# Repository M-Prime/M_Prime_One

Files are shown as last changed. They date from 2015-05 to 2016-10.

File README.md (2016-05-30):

# M Prime One

M Prime One is a free 3D printer intended to be simple, low-cost and easy to build and operate.

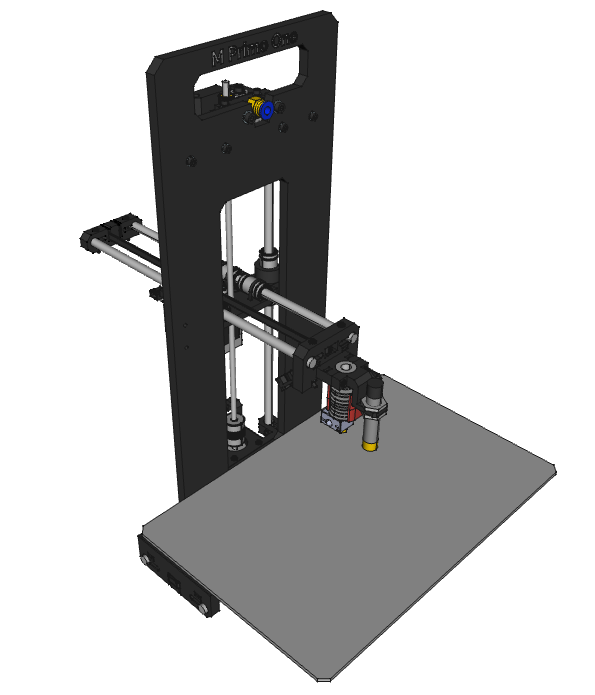
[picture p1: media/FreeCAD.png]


With the M Prime One, we have designed a 3D printer focusing on three main points:

* **Free design**. The printer have been designed from scratch in a free 3D software: FreeCAD. All the files have been published under the less restrictive license we have found (CC BY 4.0). This way anybody can download the files, modify them and use them for their own purposes.
* **Simplicity**. The design has few different parts (for example, cold bed, 4 motors, just two types of screws and one type of radial bearings) in an effort to reduce building complexity, cost and maintenance.
* **Documentation**. Apart from the files, you can find the printer firmware, list of materials, slicing profiles... in this repository, receive support in our [Q&A site](http://mprime.io/questions/) and soon read the complete assembly manual in the [manuals repository](https://github.com/M-Prime/M_Prime_One_manuals).

## Features

The features of the M Prime One are:

* Printing surface: 200x150x150mm.
* 1.75mm bowden extruder.
* Compatible with any hotend with 12mm diameter mount.
* Magnetic bed, easy to place and remove.
* Auto-level system with inductive/capacitive sensor.
* Cable management integrated in the design
* Integrated electronics holder (compatible with RAMPS, can be adapted to any other board)
* Optional LCD holder (compatible with Smart Controller)

## How to start building your M Prime One

* Download all the fabrication files (`.stl` for 3D printing and `.dxf` for laser/CNC cut) following our [fabrication file guide](documentation/fabrication_files.md).
* Check the complete part list is the Bill Of Materials, or [BOM](documentation/BOM.md).
* You can use the [assembled FreeCAD model](m_prime_one.fcstd) to help you build the machine or if you are comfortable installing modules in FreeCAD see the animated assembly files in our [manuals repository](https://github.com/M-Prime/M_Prime_One_manuals) (soon we will provide assembly videos).

And you can take a look at our [How to build an M Prime One guide](http://mprime.io/how-to-build-an-m-prime-one/), source some of the parts from our store and help the project =)

## License

The files of this 3D printer project have been released under the Creative Commons Attribution 4.0 license. This license lets you modify and share the sources for any purpose, even commercial, with the only requeriment of giving credit to the author.

Feel free to take a look at the files, modify them for your own uses, create new parts, etc. If you do so, I would be very happy if you let me know of your projects. Also, if possible, share them with the community with this or other free license.

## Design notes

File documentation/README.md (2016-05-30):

# Documentation

## Where is the Bill Of Materials

Check the complete part list is the Bill Of Materials: [BOM](documentation/BOM.md).

## Where are the fabrication files?

Download all the fabrication files (`.stl` for 3D printing and `.dxf` for laser/CNC cut) following our [fabrication file guide](documentation/fabrication_files.md).

## Assembling the M Prime One

You can use the [assembled FreeCAD model](m_prime_one.fcstd) to help you build the machine or if you are comfortable installing modules in FreeCAD see the animated assembly files in our [manuals repository](https://github.com/M-Prime/M_Prime_One_manuals) (soon we will provide assembly videos).

## Support

You can receive support from us and our community at:

* Q&A site: http://mprime.io/questions/
* Google+ community, for discussion and support: https://plus.google.com/u/0/communities/108084856251985677965

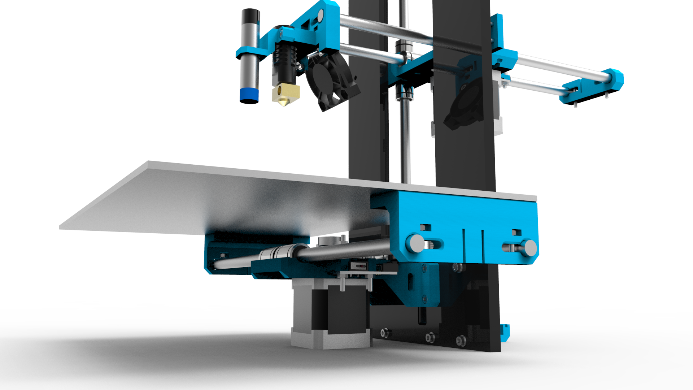
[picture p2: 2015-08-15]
media/renders_pre_v1.0/M Prime One.38.png

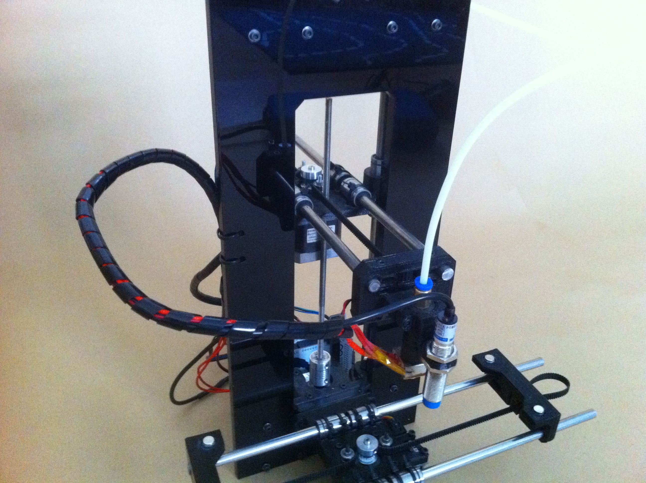
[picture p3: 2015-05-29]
media/2015-05-26 17.56.42.jpg

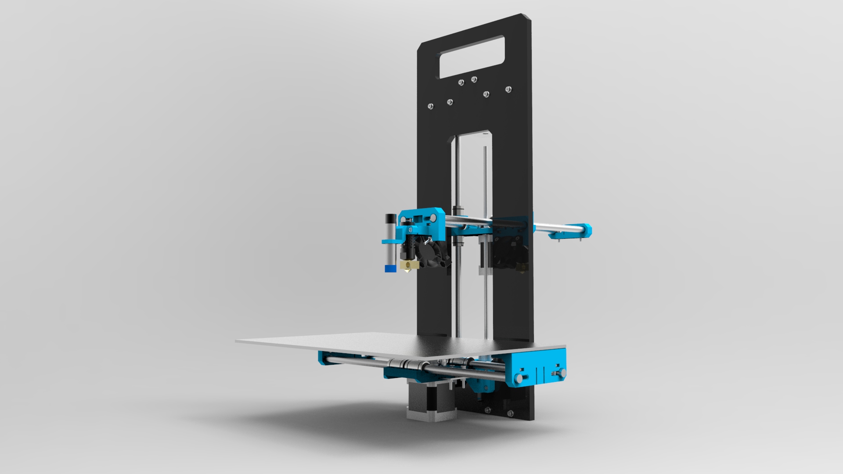
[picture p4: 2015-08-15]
media/renders_pre_v1.0/M Prime One.30.jpg

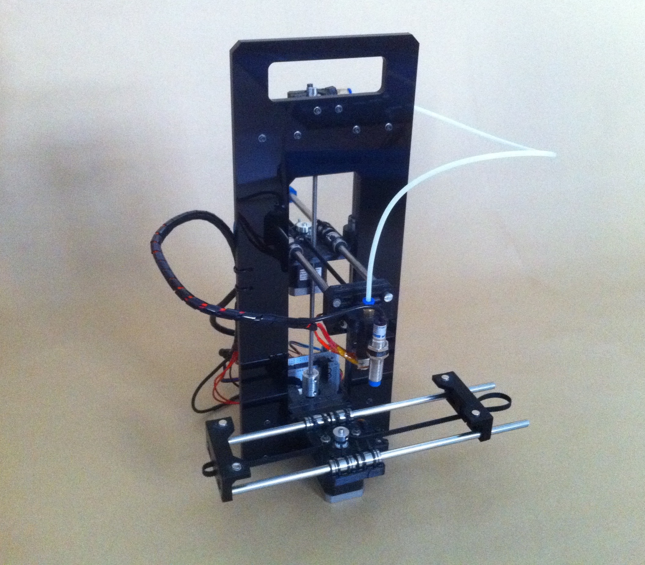
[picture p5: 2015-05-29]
media/2015-05-26 17.56.34 edited.jpg

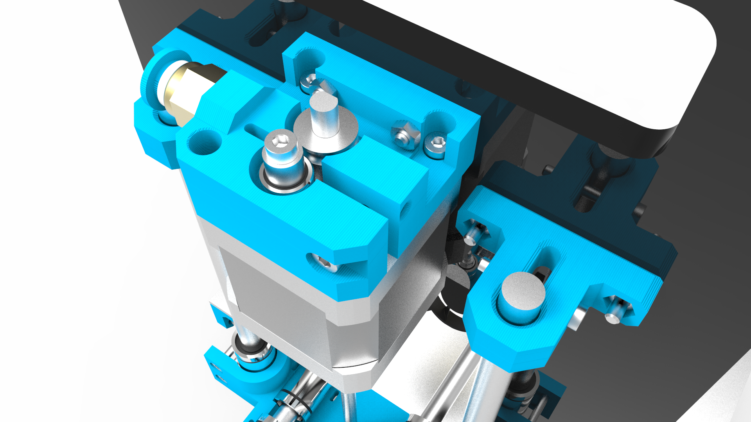
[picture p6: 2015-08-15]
media/renders_pre_v1.0/M Prime One.40.png

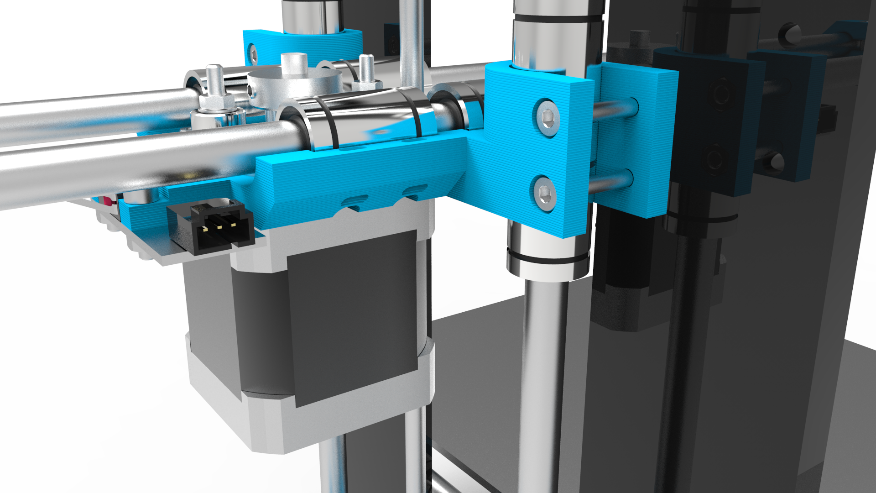
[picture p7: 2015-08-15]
media/renders_pre_v1.0/M Prime One.36.png

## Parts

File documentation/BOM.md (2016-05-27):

# M Prime One BOM

| Part | Quantity |  Unit | Notes |
| --- | --- | ----- | --- |
| NEMA 17 Motor | 4 | unit  | |
| Mechanical endstop v1.8  | 2 | unit  | |
| LM8UU linear bearing | 12 | unit  | |
| 623ZZ bearing | 9 | unit  | |
| GT2 belt | 1 | meter | |
| GT2 belt pulley | 2 | unit  | |
| Flexible shaft coupler | 1 | unit  | |
| M3x20 | 100 | unit  | More than necessary |
| M3x10 | 100 | unit  | More than necessary |
| M3 nut | 100 | unit  | More than necesary |
| M3 washer | 100 | unit  | More than necesary |
| M5 nut | 1 | unit  | |
| MK7 drive gear | 1 | unit  | |
| Bowden pneumatic fitting | 1 | unit  | Can be substituted with a M4 nut it using the hex nut version of the extruder |
| Frame | 1 | unit  | |
| Bed | 1 | unit  | 295x195x3mm aluminium/dibond plate. |
| Magnets | 4 | unit  | |
| 40x40mm fan | 1 | unit  | |
| Inductive sensor | 1 | unit  | LJ12A3-4-Z/BY |
| Rods | 1 | set | Detailed below |
| Printed parts | 1 | set | Detailed below |
| Hotend | 1 | unit  | ‎Any hotend with a Ø12mm mount should be compatible. Tested with J-Head |
| Electronics | 1 | set | |
| Power source | 1 | unit  | A 60W laptop-type power source is compact and has proven been enough |

## Rods
			
| Rods | Quantity | Length |
| --- | --- | --- |
| X 8mm smooth rod  | 2 | 300mm  |
| Y 8mm smooth rod  | 2 | 280mm  |
| Z 8mm smooth rod  | 2 | 365mm  |
| Z M5 threaded rod | 1 | 230mm  |
			
## Printed parts
	
| Printed parts | Quantity | Notes |
| --- | --- | --- |
| bowden_extruder | 1 | Use the hex nut version for attaching the bowden cable with a M4 nut |
| hotend_and_probe_holder | 1 | Needs support |
| printer_head | 1 | |
| smooth_rod_holder | 4 | |
| x_axis_end | 2 | |
| x_motor_support | 1 | |
| y_rear_end | 1 | |
| yz_carriage | 1 | Use the yz_carriage_fixed.stl file that fixes mesh problems |
| z_motor_support | 1 | |
| arduino_holder | 2 | Optional. Compatible with Arduino+RAMPS electronics |
| lcd_holder_left | 1 | Optional. Compatible with Smart Controller LCD |
| lcd_holder_right | 1 | Optional. Compatible with Smart Controller LCD |
| tool_holder | 1 | Optional. Use if you want a tool holder in the front of the printer  |

## Spreadsheet version

An online, spreadsheet version of this BOM can be accessed in the URL https://docs.google.com/spreadsheets/d/17mDN-wsaQ2GuqwfJa5OUW5vtk42V1e22lN0ufY5h_80/edit?usp=sharing. Feel free to copy the document and make your own list.

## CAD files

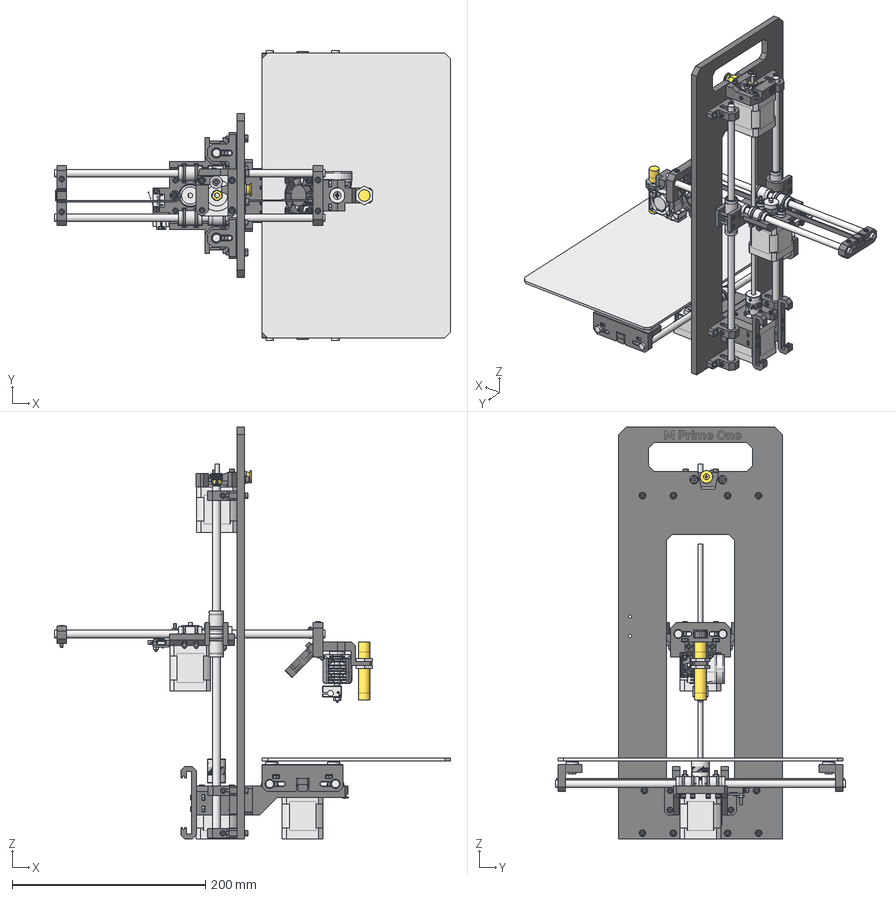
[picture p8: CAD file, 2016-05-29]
m_prime_one.fcstd
409.6 x 300.0 x 426.0 mm
nema_17_motor_01
frame_01
5x5mm_shaft_coupler_01
z_threaded_rod_01
pp_z_motor_support_01
m3x10_iso4762_bolt_01
m3x10_iso4762_bolt_02
m3x10_iso4762_bolt_03
m3x10_iso4762_bolt_04
pp_x_motor_support_01
pp_smooth_rod_holder_01
pp_smooth_rod_holder_02
m3_iso4032_nut_01
m3_iso4032_nut_02
m3_iso4032_nut_03
m3_iso4032_nut_04
m3_iso4032_nut_05
m3_iso4032_nut_06
m3_iso4032_nut_07
m3_iso4032_nut_08
m3_iso4032_nut_09
m3_iso4032_nut_10
m3_iso4032_nut_11
m3_iso4032_nut_12
m3_iso4032_nut_13
m3_iso4032_nut_14
m3_iso4032_nut_15
m3_iso4032_nut_16
m3_iso4032_nut_17
m3_iso4032_nut_18
pp_arduino_holder_01
pp_arduino_holder_02
m3_iso7089_washer_01
m3_iso7089_washer_02
m3_iso7089_washer_03
m3_iso7089_washer_04
m3_iso7089_washer_05
m3_iso7089_washer_06
m3x20_iso4762_bolt_01
m3x20_iso4762_bolt_02
m3x20_iso4762_bolt_03
m3x20_iso4762_bolt_04
m3x20_iso4762_bolt_05
m3x20_iso4762_bolt_06
m3x20_iso4762_bolt_07
m3x20_iso4762_bolt_08
m3x20_iso4762_bolt_09
m3x20_iso4762_bolt_10
m3x20_iso4762_bolt_11
m3x20_iso4762_bolt_12
m3x20_iso4762_bolt_13
m3x20_iso4762_bolt_14
z_smooth_rod_01
z_smooth_rod_02
m3x20_iso4762_bolt_15
m3x20_iso4762_bolt_16
m3x20_iso4762_bolt_17
m3x20_iso4762_bolt_18
nema_17_motor_02
m3x10_iso4762_bolt_05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

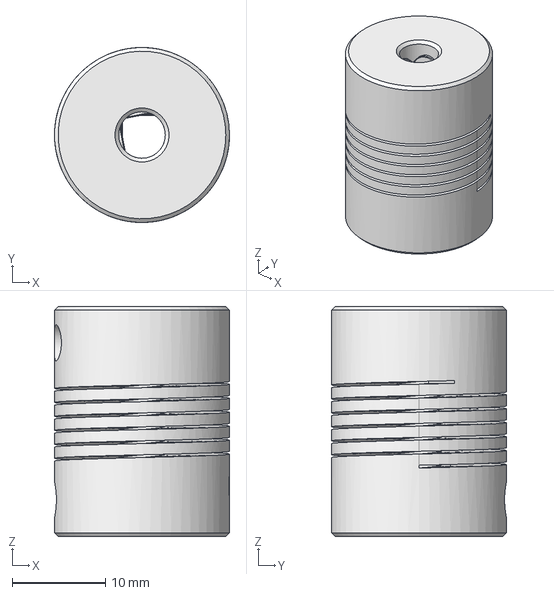
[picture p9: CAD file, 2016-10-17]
parts/5x5mm_shaft_coupler/5x5mm_shaft_coupler_views.FCStd
18.8 x 18.8 x 24.7 mm

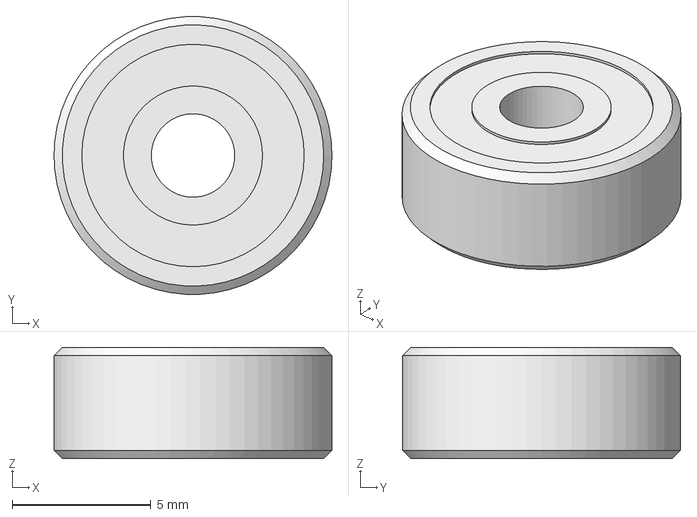
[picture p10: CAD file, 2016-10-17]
parts/623zz_bearing/623zz_bearing_views.FCStd
10.0 x 9.99 x 4.00 mm

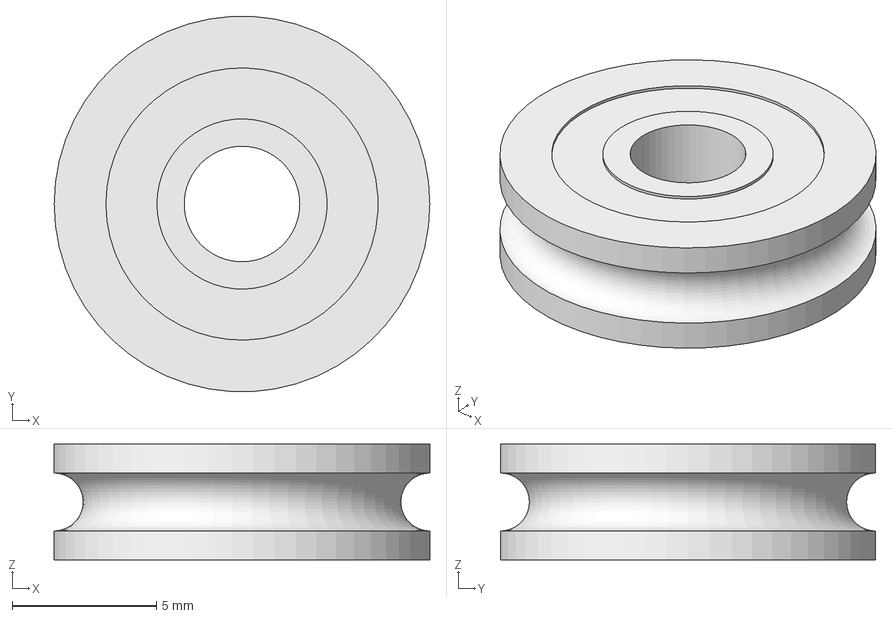
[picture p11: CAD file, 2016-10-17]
parts/624uu_bearing/624uu_bearing_views.FCStd
13.0 x 13.0 x 4.00 mm

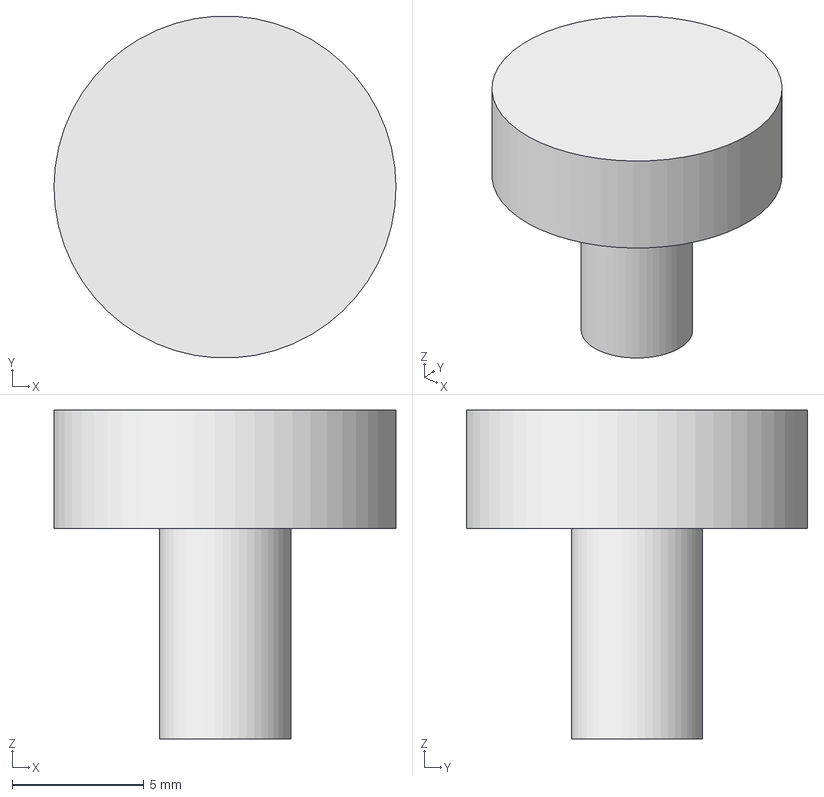
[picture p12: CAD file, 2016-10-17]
parts/bed_magnet/bed_magnet_views.FCStd
13.0 x 13.0 x 12.5 mm

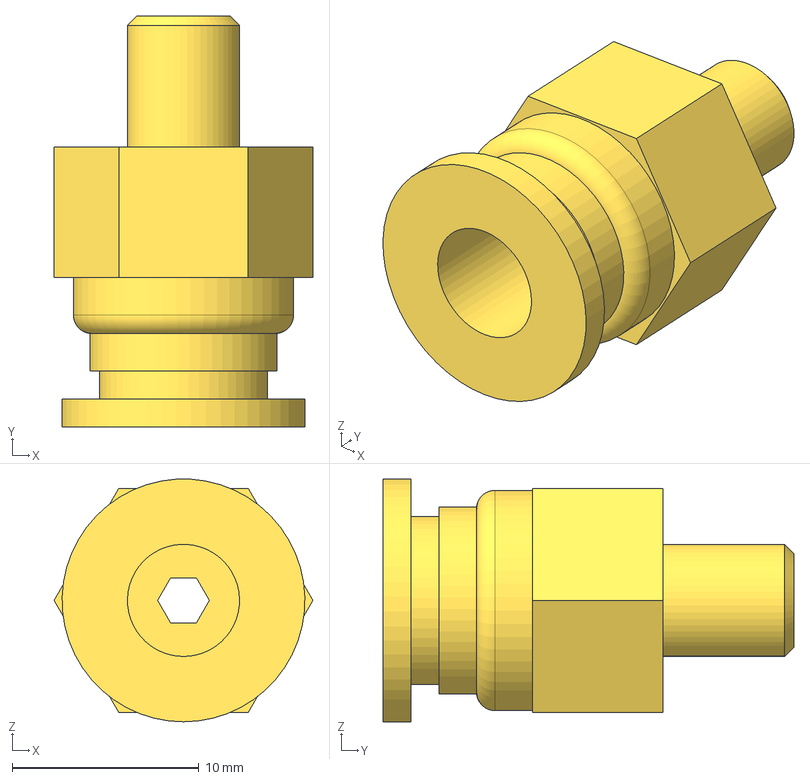
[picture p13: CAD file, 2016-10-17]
parts/bowden_fitting/bowden_fitting_views.FCStd
13.9 x 22.0 x 13.0 mm

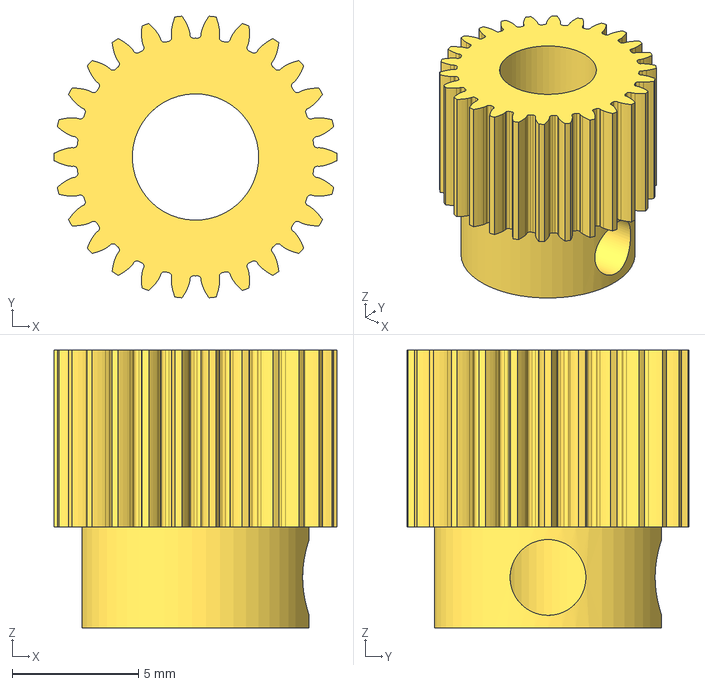
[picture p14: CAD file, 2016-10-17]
parts/drive_gear/drive_gear_views.FCStd
11.2 x 11.2 x 11.0 mm

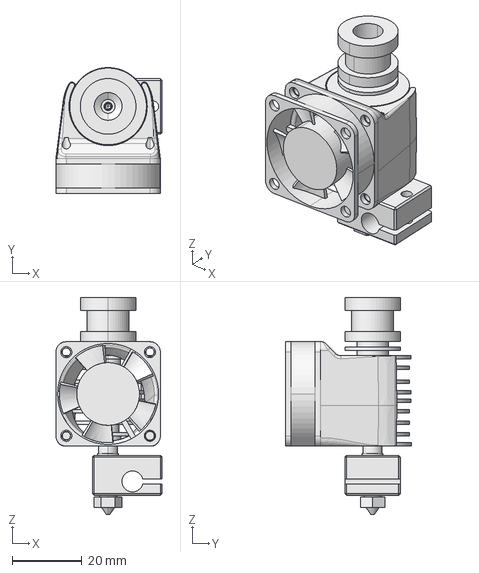
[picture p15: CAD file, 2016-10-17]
parts/e3d_lite6_hotend/e3d_lite6_hotend_views.FCStd
30.5 x 36.2 x 62.3 mm

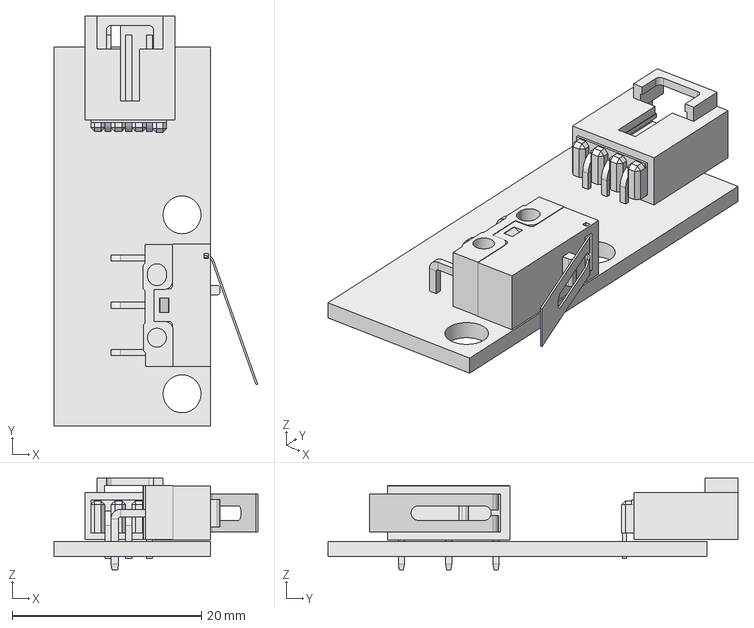
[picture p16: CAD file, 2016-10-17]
parts/endstop/endstop_views.FCStd
21.5 x 43.3 x 9.70 mm

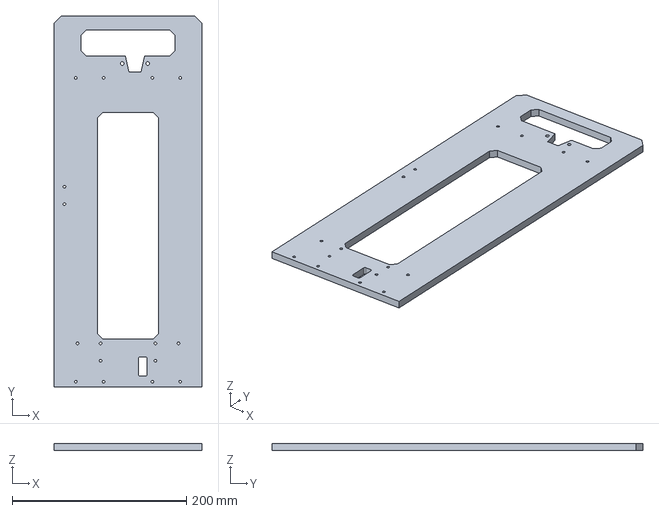
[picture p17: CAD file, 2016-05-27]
parts/frame/alternate_versions/frame_without_engraving.fcstd
170.0 x 426.0 x 8.00 mm

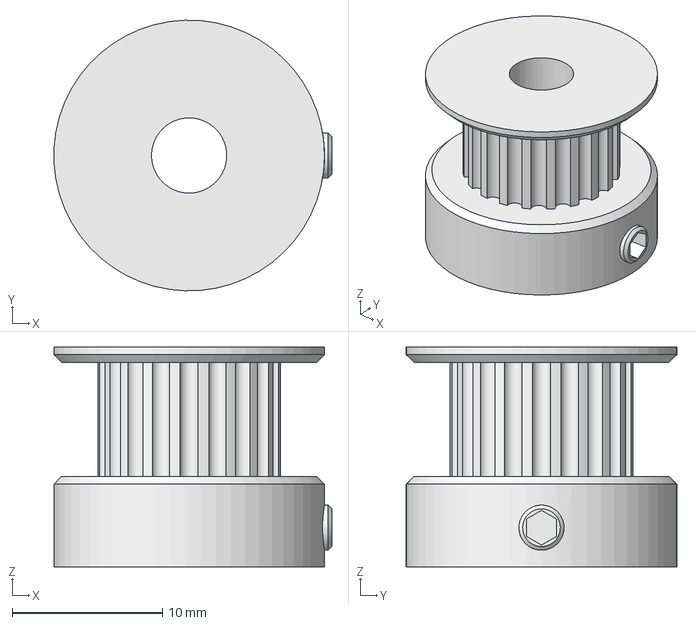
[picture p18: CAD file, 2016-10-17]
parts/gt2_pulley/gt2_pulley_views.FCStd
18.5 x 18.0 x 14.6 mm

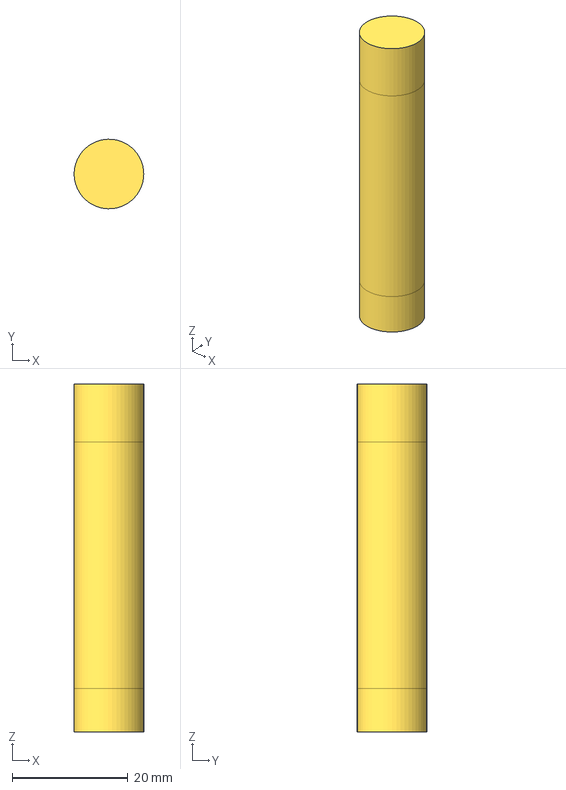
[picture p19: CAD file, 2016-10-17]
parts/inductive_sensor/inductive_sensor_views.FCStd
12.0 x 12.0 x 60.0 mm

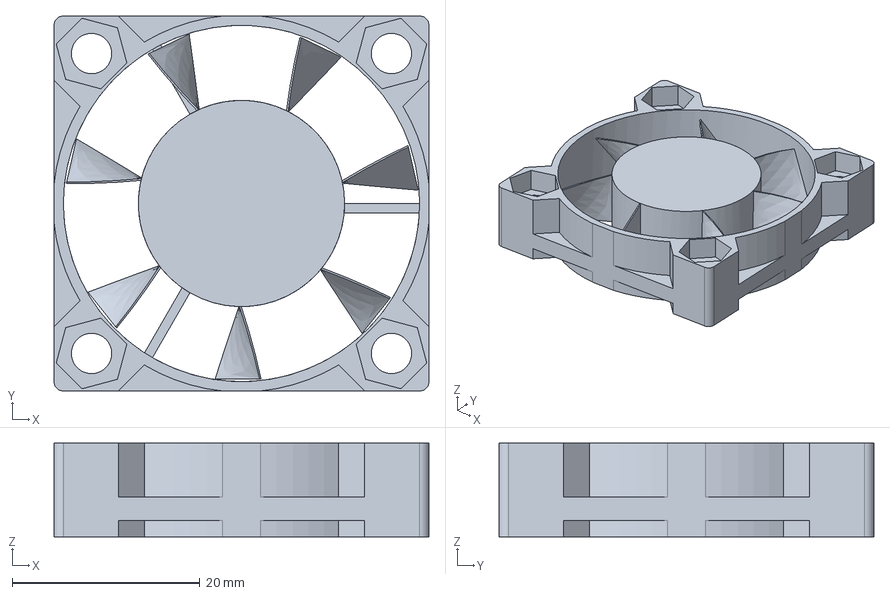
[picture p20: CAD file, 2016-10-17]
parts/layer_fan/layer_fan_views.FCStd
40.0 x 40.0 x 10.0 mm

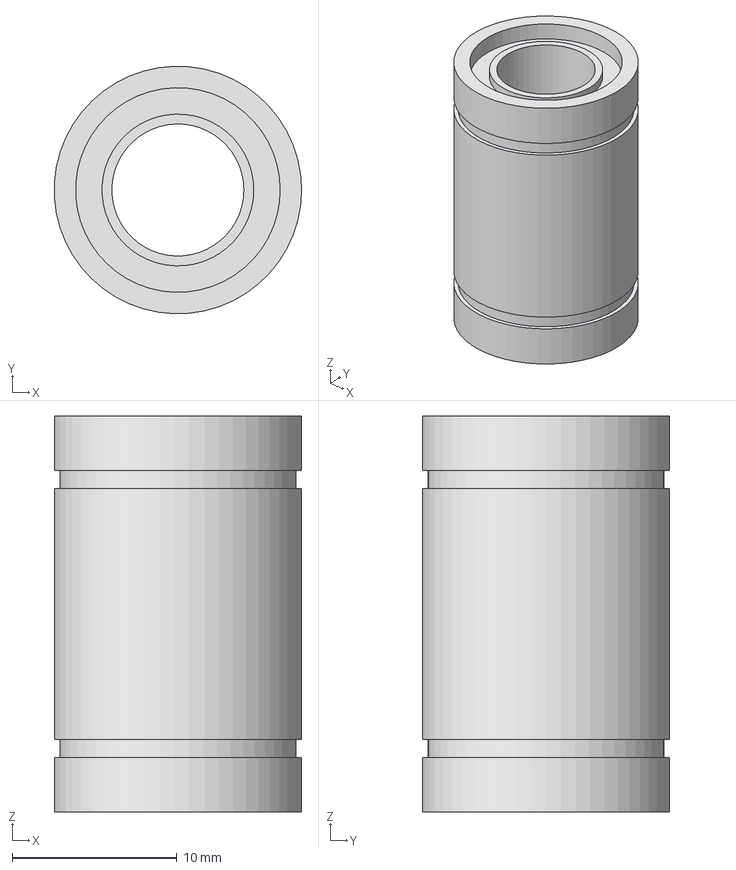
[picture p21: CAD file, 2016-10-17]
parts/lm8uu_linear_bearing/lm8uu_linear_bearing_views.FCStd
15.0 x 15.0 x 24.0 mm

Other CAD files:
parts/frame/frame_views.FCStd
parts/nema_17_motor/nema_17_motor_views.FCStd
parts/pp_arduino_holder/pp_arduino_holder_views.FCStd
parts/pp_hotend_and_probe_holder/pp_hotend_and_probe_holder_views.FCStd
parts/5x5mm_shaft_coupler/5x5mm_shaft_coupler.fcstd
parts/623zz_bearing/623zz_bearing.fcstd
parts/624uu_bearing/624uu_bearing.fcstd
parts/bed_magnet/bed_magnet.fcstd
parts/bowden_fitting/bowden_fitting.fcstd
parts/drive_gear/drive_gear.fcstd
parts/e3d_lite6_hotend/e3d_lite6_hotend.fcstd
parts/endstop/endstop.fcstd
parts/frame/alternate_versions/frame_without_engraving.dxf
parts/frame/frame.dxf
parts/frame/frame.fcstd
parts/gt2_pulley/gt2_pulley.fcstd
parts/inductive_sensor/inductive_sensor.fcstd
parts/inductive_sensor_nut/inductive_sensor_nut.fcstd
parts/inductive_sensor_nut/inductive_sensor_nut_views.FCStd
parts/layer_fan/layer_fan.fcstd
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

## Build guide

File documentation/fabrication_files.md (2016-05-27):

# M Prime One fabrication files

This is a document to help you find all the fabrication files in the M Prime One repository, files that are used to produce some of the parts of the printer: the printed parts and the files for laser cutting or routing the frame and the bed.

All the files are located in the `parts` directory of this repository, this file only contains all the links in one place. 

## Printed parts

All the printed parts are under the `parts` directories in the subdirectories that contain the prefix "pp_". There are also some optional parts that you can find in the `parts_optional` directory, including a beta bowden extruder that you can try if you don't want to use the PTSone extruder (however the extruder hasn't been fully tested and we cannot guarantee that it will perform reliably). We provide `.stl` files for the printed parts.

This is the list of the M Prime One printed parts:

* Arduino holder: [pp_arduino_holder](../parts/pp_arduino_holder) 
* Hotend and probe holder: [pp_hotend_and_probe_holder](../parts/pp_hotend_and_probe_holder) 
* Printer head: [pp_printer_head](../parts/pp_printer_head) 
* Smooth rod holder: [pp_smooth_rod_holder](../parts/pp_smooth_rod_holder) 
* X axis end: [pp_x_axis_end](../parts/pp_x_axis_end) 
* X motor support: [pp_x_motor_support](../parts/pp_x_motor_support) 
* Y rear end: [pp_y_rear_end](../parts/pp_y_rear_end) 
* YZ carriage: [pp_yz_carriage](../parts/pp_yz_carriage) 
* Z motor support: [pp_z_motor_support](../parts/pp_z_motor_support) 

## Laser cut or CNC routed parts

There are two parts that can be made in a laser cutter or in a CNC router. We provide `.dxf` files for them:

* Frame: [frame files](../parts/frame)
* Printing surface: [printing surface files](../parts/printing_surface)

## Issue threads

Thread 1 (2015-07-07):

Rapid wear of the z axis screw and nut

diegotrap, 2015-07-07:
The z axis threaded rod and nut system wears out very fast, due to the autoleveling feature that keeps it moving during all the printing time. In a controlled test it started giving problems after just 15 hours of printing.

The wearing of the axis causes backlash, formation of metal dust that eventually jams the axis and finally the definitive wearing of the nut and rod threads, the rod no longer holds the nut.

Temporary solutions for this issue are:
* Lubricating the rod
* Changing the nut
* Flipping the threaded rod
* Changing the threaded rod

I am trying to change the stainles steel nut for other materials: nylon and brass. I'll report on my experiments.

diegotrap, 2015-09-05:
The problem has been solved by using a nylon nut. They don't show signs of wear off and they are also easier to change than the whole rod-nut combination.

Closed 2015-09-05.

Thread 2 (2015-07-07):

Reliability of the extruder

diegotrap, 2015-07-07:
The default 3D printed extruder (not to be confused with hotend) have been tested and can deliver quality prints, but it starts to give problems after some time (in my case, days/weeks of moderate use). I think the plastic starts to deform after being near the hot motor for some time.

I have bypassed this problem by using a metal extruder, but it would be good for the project to develop a more reliable, 3d printed extruder. I will also try to make it compatible with my current metal extruder, so users can choose between the two options.

tcaer, 2016-03-01:
Hi Diego, is there any way we can create the metal extruder ourselves?
Thanks

diegotrap, 2016-03-01:
You can develop a metal extruder or copy the design that I actually have. However I don't have the plans and it is designed to be casted, not machined.

A metal extruder or a more reliable printed one is in my plans, but I have not found time to design it, so it is an issue that may not be fixed in the near future.

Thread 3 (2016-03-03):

unusable frame format (DXF) no STEP OR OTHER usable files attached

inkjunkies, 2016-03-03:
good luck trying to convert this file to something usable

diegotrap, 2016-03-04:
I think all the files are usable, I have tested myself and found no problems. Maybe the problems come from your setup, but if you give us more information we can try to fix it:

* I have downloaded the repo, and opened the file with LibreCAD, I haven't found any problem. The problem may exist and other users have reported similar issues, but please give us more information about the error so we can try to fix it.
* Currently we do not provide .step files, only the FreeCAD and fabrication (.dxf, .stl) files. I consider FreeCAD files usable, since you can open them in any platform and export them to many other formats. I have also taken my time to open a part in FreeCAD, export to .step and then open the file (in both FreeCAD and Adobe Fusion 360) and haven't found any problem with that. If you give us more information about this issue maybe we can fix it.

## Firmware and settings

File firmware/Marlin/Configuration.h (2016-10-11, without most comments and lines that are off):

#define CONFIGURATION_H
#define CONFIGURATION_H_VERSION 010100
#define STRING_CONFIG_H_AUTHOR "(M Prime)" // Who made the changes.
#define SHOW_BOOTSCREEN
#define STRING_SPLASH_LINE1 SHORT_BUILD_VERSION // will be shown during bootup in line 1
#define STRING_SPLASH_LINE2 "http://mprime.io"         // will be shown during bootup in line 2
#define SERIAL_PORT 0
#define BAUDRATE 250000
  #define MOTHERBOARD BOARD_RAMPS_14_EFB
#define CUSTOM_MACHINE_NAME "M Prime One"
#define EXTRUDERS 1
#define POWER_SUPPLY 1
#define TEMP_SENSOR_0 5
#define TEMP_SENSOR_1 0
#define TEMP_SENSOR_2 0
#define TEMP_SENSOR_3 0
#define TEMP_SENSOR_BED 0
#define MAX_REDUNDANT_TEMP_SENSOR_DIFF 10
#define TEMP_RESIDENCY_TIME 10  // (seconds)
#define TEMP_HYSTERESIS 3       // (degC) range of +/- temperatures considered "close" to the target one
#define TEMP_WINDOW     1       // (degC) Window around target to start the residency timer x degC early.
#define TEMP_BED_RESIDENCY_TIME 10  // (seconds)
#define TEMP_BED_HYSTERESIS 3       // (degC) range of +/- temperatures considered "close" to the target one
#define TEMP_BED_WINDOW     1       // (degC) Window around target to start the residency timer x degC early.
#define HEATER_0_MINTEMP 5
#define HEATER_1_MINTEMP 5
#define HEATER_2_MINTEMP 5
#define HEATER_3_MINTEMP 5
#define BED_MINTEMP 5
#define HEATER_0_MAXTEMP 245
#define HEATER_1_MAXTEMP 245
#define HEATER_2_MAXTEMP 245
#define HEATER_3_MAXTEMP 245
#define BED_MAXTEMP 150
#define PIDTEMP
#define BANG_MAX 180 // limits current to nozzle while in bang-bang mode; 255=full current
#define PID_MAX BANG_MAX // limits current to nozzle while PID is active (see PID_FUNCTIONAL_RANGE below); 255=full current
  #define PID_FUNCTIONAL_RANGE 10 // If the temperature difference between the target temperature and the actual temperature
  #define PID_INTEGRAL_DRIVE_MAX PID_MAX  //limit for the integral term
  #define K1 0.95 //smoothing factor within the PID
    #define  DEFAULT_Kp 27.96
    #define  DEFAULT_Ki 2.02
    #define  DEFAULT_Kd 96.87
#define MAX_BED_POWER 255 // limits duty cycle to bed; 255=full current
#define PREVENT_DANGEROUS_EXTRUDE
#define PREVENT_LENGTHY_EXTRUDE
#define EXTRUDE_MINTEMP 170
#define EXTRUDE_MAXLENGTH (X_MAX_LENGTH+Y_MAX_LENGTH) //prevent extrusion of very large distances.
#define THERMAL_PROTECTION_HOTENDS // Enable thermal protection for all extruders
#define THERMAL_PROTECTION_BED     // Enable thermal protection for the heated bed
#define USE_YMIN_PLUG
#define USE_ZMIN_PLUG
#define USE_XMAX_PLUG
#define ENDSTOPPULLUPS // Comment this out (using // at the start of the line) to disable the endstop pullup resistors
#define X_MIN_ENDSTOP_INVERTING true // set to true to invert the logic of the endstop.
#define Y_MIN_ENDSTOP_INVERTING true // set to true to invert the logic of the endstop.
#define Z_MIN_ENDSTOP_INVERTING true // set to true to invert the logic of the endstop.
#define X_MAX_ENDSTOP_INVERTING true // set to true to invert the logic of the endstop.
#define Y_MAX_ENDSTOP_INVERTING true // set to true to invert the logic of the endstop.
#define Z_MAX_ENDSTOP_INVERTING true // set to true to invert the logic of the endstop.
#define Z_MIN_PROBE_ENDSTOP_INVERTING true // set to true to invert the logic of the endstop.
#define FIX_MOUNTED_PROBE
#define X_PROBE_OFFSET_FROM_EXTRUDER 0  // X offset: -left  +right  [of the nozzle]
#define Y_PROBE_OFFSET_FROM_EXTRUDER -24  // Y offset: -front +behind [the nozzle]
#define Z_PROBE_OFFSET_FROM_EXTRUDER 0   // Z offset: -below +above  [the nozzle]
#define XY_PROBE_SPEED 3000
#define Z_PROBE_SPEED_FAST HOMING_FEEDRATE_Z
#define Z_PROBE_SPEED_SLOW (Z_PROBE_SPEED_FAST / 2)
#define PROBE_DOUBLE_TOUCH
#define Z_MIN_PROBE_USES_Z_MIN_ENDSTOP_PIN
#define Z_MIN_PROBE_REPEATABILITY_TEST
#define Z_PROBE_DEPLOY_HEIGHT 5 // Raise to make room for the probe to deploy / stow
#define Z_PROBE_TRAVEL_HEIGHT 3  // Raise between probing points.
#define Z_PROBE_OFFSET_RANGE_MIN -20
#define Z_PROBE_OFFSET_RANGE_MAX 20
#define X_ENABLE_ON 0
#define Y_ENABLE_ON 0
#define Z_ENABLE_ON 0
#define E_ENABLE_ON 0 // For all extruders
#define DISABLE_X false
#define DISABLE_Y false
#define DISABLE_Z false
#define DISABLE_E false // For all extruders
#define DISABLE_INACTIVE_EXTRUDER true //disable only inactive extruders and keep active extruder enabled
#define INVERT_X_DIR false
#define INVERT_Y_DIR false
#define INVERT_Z_DIR true
#define INVERT_E0_DIR true
#define INVERT_E1_DIR false
#define INVERT_E2_DIR false
#define INVERT_E3_DIR false
#define X_HOME_DIR 1
#define Y_HOME_DIR -1
#define Z_HOME_DIR -1
#define min_software_endstops false // If true, axis won't move to coordinates less than HOME_POS.
#define max_software_endstops true  // If true, axis won't move to coordinates greater than the defined lengths below.
#define X_MIN_POS 0
#define Y_MIN_POS 0
#define Z_MIN_POS 0
#define X_MAX_POS 200
#define Y_MAX_POS 150
#define Z_MAX_POS 150
#define AUTO_BED_LEVELING_FEATURE // Delete the comment to enable (remove // at the start of the line)
  #define AUTO_BED_LEVELING_GRID
    #define LEFT_PROBE_BED_POSITION 50
    #define RIGHT_PROBE_BED_POSITION 150
    #define FRONT_PROBE_BED_POSITION 5
    #define BACK_PROBE_BED_POSITION 110
    #define MIN_PROBE_EDGE 10 // The Z probe minimum square sides can be no smaller than this.
    #define AUTO_BED_LEVELING_GRID_POINTS 2
#define Z_SAFE_HOMING
  #define Z_SAFE_HOMING_X_POINT ((X_MIN_POS + X_MAX_POS) / 2)    // X point for Z homing when homing all axis (G28).
  #define Z_SAFE_HOMING_Y_POINT ((Y_MIN_POS + Y_MAX_POS) / 2)    // Y point for Z homing when homing all axis (G28).
#define HOMING_FEEDRATE_XY (50*60)
#define HOMING_FEEDRATE_Z  (2*60)
#define DEFAULT_AXIS_STEPS_PER_UNIT   {80,80,4000,104}  // default steps per unit for Ultimaker
#define DEFAULT_MAX_FEEDRATE          {200, 200, 5, 25}    // (mm/sec)
#define DEFAULT_MAX_ACCELERATION      {3000,3000,100,10000}    // X, Y, Z, E maximum start speed for accelerated moves. E default values are good for Skeinforge 40+, for older versions raise them a lot.
#define DEFAULT_ACCELERATION          3000    // X, Y, Z and E acceleration in mm/s^2 for printing moves
#define DEFAULT_RETRACT_ACCELERATION  3000    // E acceleration in mm/s^2 for retracts
#define DEFAULT_TRAVEL_ACCELERATION   3000    // X, Y, Z acceleration in mm/s^2 for travel (non printing) moves
#define DEFAULT_XYJERK                15.0    // (mm/sec)
#define DEFAULT_ZJERK                 0.4     // (mm/sec)
#define DEFAULT_EJERK                 5.0    // (mm/sec)
#define EEPROM_SETTINGS
  #define EEPROM_CHITCHAT // Please keep turned on if you can.
#define HOST_KEEPALIVE_FEATURE        // Disable this if your host doesn't like keepalive messages
#define DEFAULT_KEEPALIVE_INTERVAL 2  // Number of seconds between "busy" messages. Set with M113.
#define PREHEAT_1_TEMP_HOTEND 200
#define PREHEAT_1_TEMP_BED      0
#define PREHEAT_1_FAN_SPEED     0 // Value from 0 to 255
#define PREHEAT_2_TEMP_HOTEND 240
#define PREHEAT_2_TEMP_BED      0
#define PREHEAT_2_FAN_SPEED     0 // Value from 0 to 255
#define PRINTJOB_TIMER_AUTOSTART
#define PRINTCOUNTER
#define LCD_LANGUAGE es
#define DISPLAY_CHARSET_HD44780 JAPANESE
#define ULTRA_LCD   // Character based
#define SDSUPPORT
#define REVERSE_ENCODER_DIRECTION
#define SPEAKER
#define REPRAP_DISCOUNT_SMART_CONTROLLER
#define SOFT_PWM_SCALE 0
#define SERVO_DELAY 300
#define DEFAULT_NOMINAL_FILAMENT_DIA 3.00  //Enter the diameter (in mm) of the filament generally used (3.0 mm or 1.75 mm) - this is then used in the slicer software.  Used for sensor reading validation

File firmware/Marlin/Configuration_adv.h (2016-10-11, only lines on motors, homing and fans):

#define CONTROLLERFAN_PIN -1 //Pin used for the fan to cool controller (-1 to disable)
#define EXTRUDER_0_AUTO_FAN_PIN 8
#define EXTRUDER_1_AUTO_FAN_PIN -1
#define EXTRUDER_2_AUTO_FAN_PIN -1
#define EXTRUDER_3_AUTO_FAN_PIN -1
#define X_HOME_BUMP_MM 5
#define Y_HOME_BUMP_MM 5
#define Z_HOME_BUMP_MM 2
#define HOMING_BUMP_DIVISOR {2, 2, 4}  // Re-Bump Speed Divisor (Divides the Homing Feedrate)
#define MICROSTEP_MODES {16,16,16,16,16} // [1,2,4,8,16]
#define DIGIPOT_MOTOR_CURRENT {135,135,135,135,135} // Values 0-255 (RAMBO 135 = ~0.75A, 185 = ~1A)
#define DIGIPOT_I2C_MOTOR_CURRENTS {1.0, 1.0, 1.0, 1.0, 1.0, 1.0, 1.0, 1.0}

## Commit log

2015-06-14 New hotend and probe holder
    Longer probe holder that achieves compatibility with the e3D lite6
    hotend.
    [hotend_and_probe_holder.fcstd, hotend_and_probe_holder.stl]
2015-06-15 SAV Mk1 electronics holder
    Added compatibility with the SAV Mk1 electronics board
    [sav_holder.fcstd, sav_holder.stl]
2015-06-16 Uploaded a fixed version of the x_axis_end
    [x_axis_end_fixed.stl]
2015-06-16 Corrected the name of the yz_carriage in the BOM
2015-06-18 Reorganized the printed_parts directory and added auxiliary files
    I’ve reorganized the printed_parts directory, using subdirectories for
    helping users choose which parts to download and print.
    Also, I have added the auxiliary files I’ve used in the design of the
    printer parts, so anyone can fully modify the objects. These files are
    marked with aux_ in the filename.
    [arduino_holder.fcstd, arduino_holder.stl, aux_LM8UU_holder.FCStd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]
2015-06-18 Spelling error correction
    [tool_holder.fcstd, tool_holder.stl]
2015-06-18 Added a printed_parts readme to help choose the parts
2015-06-20 Updated the tool holder
    Updated tool holder with a more useful model, also with the blank part
    so users can adapt the tool holder to their necessities.
    [tool_holder.fcstd, tool_holder.stl, tool_holder_blank.fcstd]
2015-08-21 Help for NPN/PNP sensors
    Added comment to help choose the z_min endstop inverter setting
    [Configuration.h]
2015-11-25 New version of the printer_head
    Small modifications to improve the design of the printer head:
    - Changed fan inclination to 45 degrees to direct more air flow to the
    printed part
    - Added nuts to the hotend holder. Bolts no longer screw to the plastic.
    [aux_fan_mockup.fcstd, aux_hotend_mount.fcstd, printer_head.fcstd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]
2015-12-14 Fixed and improved Configuration.h file
    * New printing limits, now they make use of the full printing surface
    * New probing points
    * Selected the e3D lite6 thermistor for extruder 0
    * Inverted the E0 axis direction so all connectors are plugged to the
    board in the same orientation
    [Configuration.h]
2016-01-05 Reduced hotted maximum temperature
    Reduced heater 0 (hotend) maxtemp to comply with the recommended
    maximum temperature for the e3d lite6 hotted.
    [Configuration.h]
2016-01-05 Restricted hotend maximum power
    Restricted the current to the hotend to 150 (max is 255), recommended
    setting for e3d lite6
    [Configuration.h]
2016-01-07 Added custom PID settings
    Custom PID settings, calculated using the Marlin autotune function. For
    use with the M Prime One and e3d Lite6 hotted.
    [Configuration.h]
2016-01-07 Less Z_RAISE_BEFORE_PROBING to enable faster bed leveling
    [Configuration.h]
2016-01-15 Improved y_rear_end
    Added double belt holder for better gripping of the belt
    [y_rear_end.fcstd, y_rear_end.stl]
2016-02-24 Changed X and Y endstop inverting setting
    Changed X and Y endstop inverting setting so it works out of the box
    with most endstop models, that use a normally open line.
    [Configuration.h]
2016-02-25 Uploaded M Prime One printed parts sheet
2016-05-27 Big commit to reach version 1.0
    This commit uploads a lot of changes in the machine and the repository
    structure to reach version 1.0 of the M Prime One project.
    We have make some improvements and evolutions on the machine:
    * New frame, directly compatible with the PTSone extruder (the new
    default extruder).
    * New 3D printed extruder, interchangeable with the PTSone all metal
    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
    [5x5mm_shaft_coupler.fcstd, 623zz_bearing.fcstd, 624uu_bearing.fcstd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]
2016-05-29 Added PTSone fixing bolts
    Added the missing PTSone fixing bolts, M4x14 bolt and M4 washers.
    [m4_iso7089_washer.fcstd, m4x14_iso4762_bolt.fcstd, m5_iso7089_washer.fcstd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]
2016-08-29 Generated pp_y_rear_end stl files
    The STL file for pp_y_rear_end were missing, I generated them.
    [pp_y_rear_end.stl]
2016-10-11 Updated firmware to Marlin RC7
    [Configuration.h, Configuration_adv.h]
2016-10-17 Added svg drawings of all parts
    We have uploaded svg drawings of every component of the printer, that
    we use to generate documentation for the project.
    [5x5mm_shaft_coupler_views.FCStd, 623zz_bearing_views.FCStd, 624uu_bearing_views.FCStd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]

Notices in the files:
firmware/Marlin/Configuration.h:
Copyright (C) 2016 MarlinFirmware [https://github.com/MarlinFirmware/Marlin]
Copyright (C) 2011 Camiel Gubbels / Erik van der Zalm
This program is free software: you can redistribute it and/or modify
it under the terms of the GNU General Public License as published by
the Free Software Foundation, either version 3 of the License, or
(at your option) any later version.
